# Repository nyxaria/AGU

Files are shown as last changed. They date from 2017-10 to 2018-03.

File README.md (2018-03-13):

# Autonomous Growing Unit

In this project I set out to create a robot that autonimously takes care of plants.<br>
The main goal was to learn as much as possible in as many areas I could, including software, hardware, electronics, CAD and even editing.

project video (https://vimeo.com/259930006)
<br><br>

Project Overview
----------------
The project is made up of 3 layers: The Android (High-level instructions), RaspberryPi 3 (High-level interpreter of instructions), and Arduino Mega (Low-level hardware controller).



The Android application is a simple UI composed of a rectangular 'garden' view where the user can add pots, and a 'seedbank' view where the user can select which seeds are in the physical trays of the machine. This application then communictes via Bluetooth with the RaspberryPi 3 [RPI], sending the raw data that the user put in. (Java)


<br><br>
The RPI acts as the brian of the operation, converting the high level abstracted instructions from the Android application into sequences of low level instructions, similar to GCODE, that the Arduino carries out one after another. It does this via scheduled timers as well as based on sensor data, such as the humidity soil sensor, depending on the plant.
It also makes a height map every day to monitor growth, personalise watering for each plant via plant-specific data scraped from a website (see Utility Programs.) (Python)
<br><br>
The Arduino firmware is the most low level code in this whole project, with the purpose of controlling the stepper motors on the gantry and probe, read end-stops, and turn the 2 pumps on/off. It communicates via the I2C bus with the Raspberry Pi 3, which acts as the brains of this build. (C++)

CAD
---
During this project I learnt to use Inventor, Fusion360, EAGLE as well as Fritzing. In the end, I ended up using Inventor instead of Fusion360 for the 3D model as it felt more natural to me (and more powerful) but used Fritzing and Eagle for the electronics diagram and schematic, respectively.

Model can be viewed online at https://skfb.ly/6vAEX.


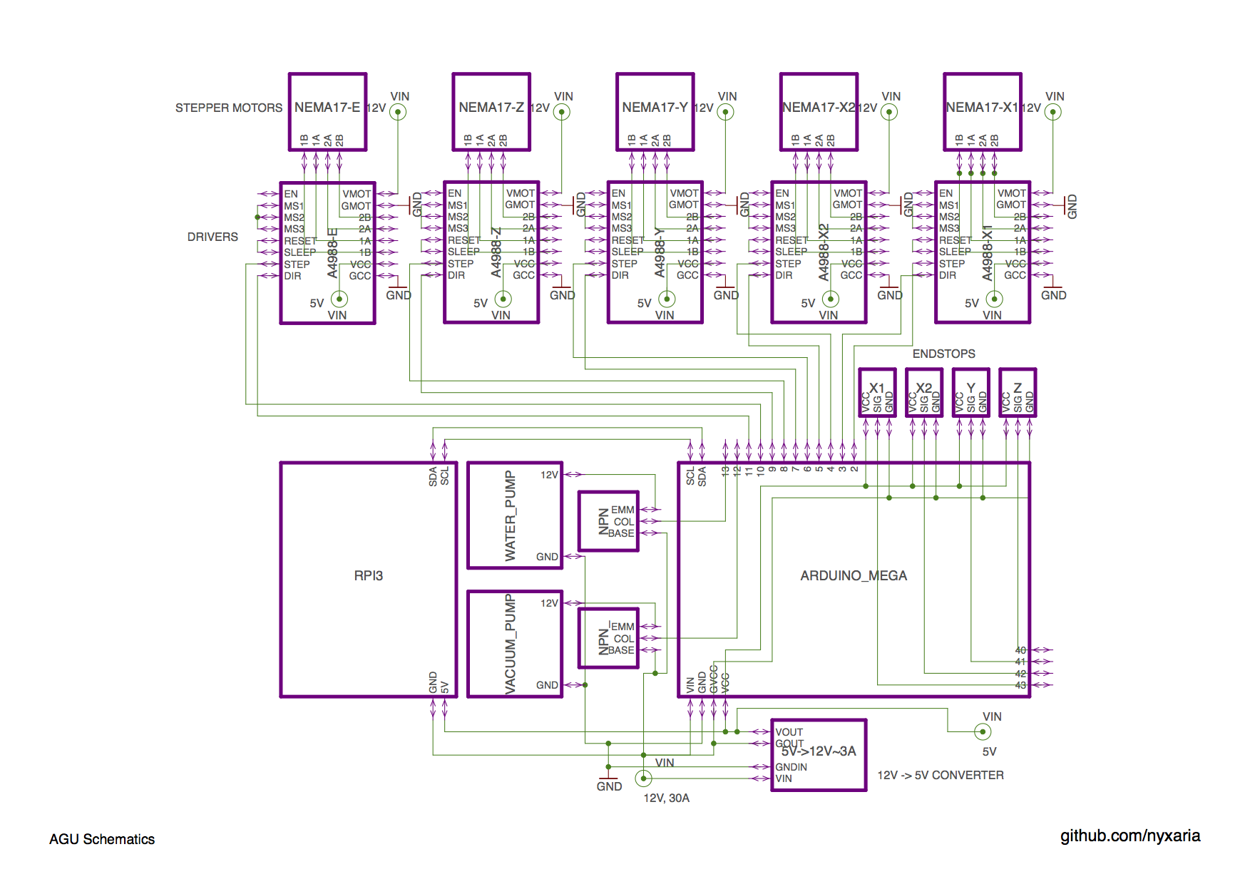
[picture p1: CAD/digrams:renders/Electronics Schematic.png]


Software
---

In this regard, I had alot of freedom in how I wanted to implement this. I ended up using an Arduino Mega because of the speed at which it alowed me to prototype, and the relative simplicity of the C++. In a future project, however, I will probably use an 8051/PIC/vanilla Atmel microcontroller and use Assembly or embedded C, not because I like self-inflicted pain but because it seems the only natural step in moving away from the 'hobby electronics' world. 
<br>In another direction I could use a ESP32 with it's Wifi+BT capabilities, and potentially eliminate the RPI entirely.
<br><br>
For the interface of the project I decided to make an Android application in Java (none of that Ionic nonsense) to brush up on my skills, but it could easily have been a Web interface written in JS+Html+Css for the UI and Flask+Py on the back end.

Hardware
---

I managed to get Makerbeams for free from my friend, so I used them for the construction. To hold everything together, I used tie plates from home depot. Everything else is held together by hot glue. For motion, I used bearings for z and x axis, and leadscrew for the y axis.

In this project I used Nema17 stepper motors which I managed to get for a really good price second hand. For the fluid transfer, I used a water pump from a coffee-machine and a vacuum pump from I ordered from China. The Mosfets and other components I scavenged from old electronics I got my hands on.

Electronics
---

I first created a schematic for project, and was planning on etching the PCB for the board containing the stepper motor drivers. However, none of the printers I have used to print the schematics on the toner-transfer paper in New York worked with the photo-transfer method. I presume it was because they were all Brother printers. As a result of that, I instead used a perf-board to make the driver break-out board.

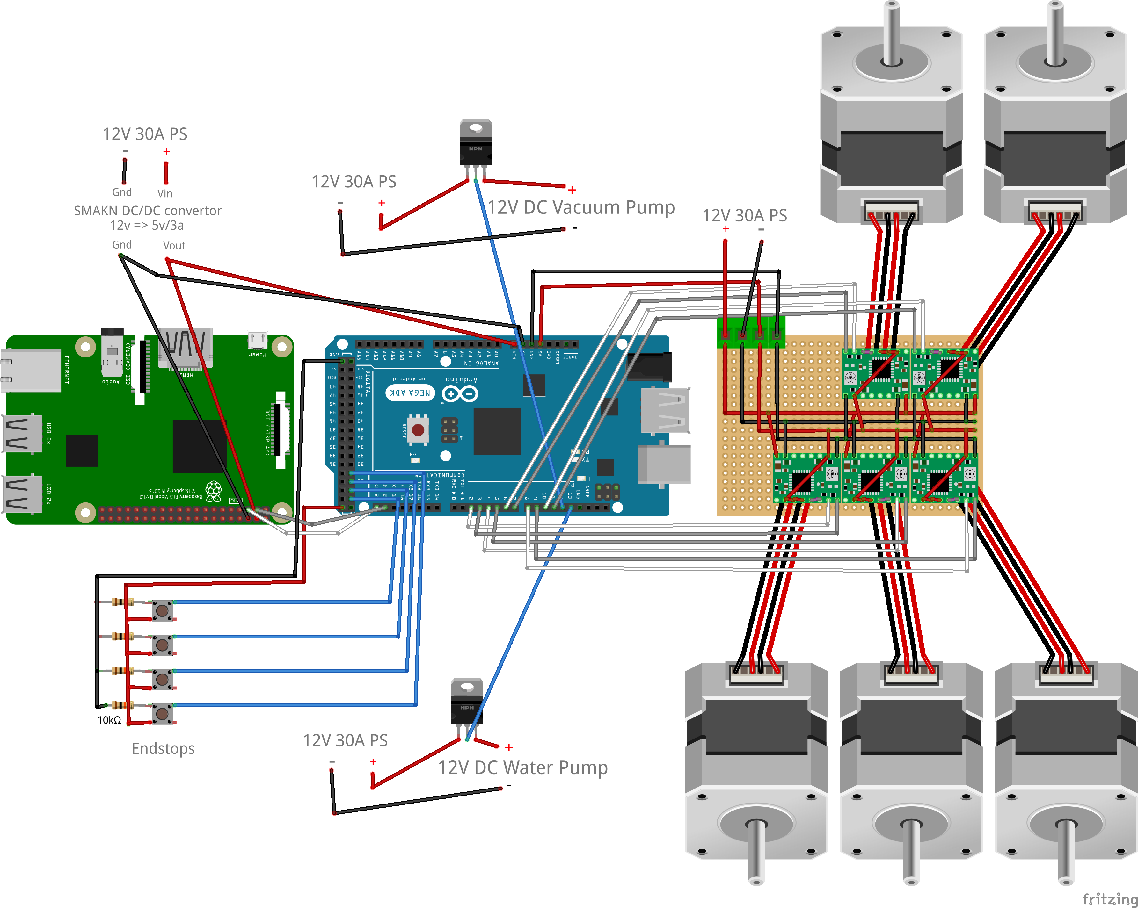
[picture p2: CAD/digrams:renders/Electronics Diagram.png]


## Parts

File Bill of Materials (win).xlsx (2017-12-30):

AGU Costs
Name | Link | Amount paid($) | Actual Cost ($) | Sum ($)
 | Electronics
Power cord | https://www.amazon.com/gp/product/B0022NH7G8/ref=oh_aui_detailpage_o06_s01?ie=UTF8&psc=1 | 8.77 |  | 240.71
12V30A PS | https://www.amazon.com/gp/product/B00D7CWSCG/ref=oh_aui_detailpage_o06_s01?ie=UTF8&psc=1 | 19.96
Arduino Mega 2560 + shield | https://www.ebay.com/itm/Arduino-Mega-2560-Board-with-Sensor-Shield-v2-0-Brand-New-Fast-Shipping/222626033269 | (Owned) | 14.24
12V -> 5V DC/DC converter | https://www.amazon.com/gp/product/B00CXKBJI2/ref=oh_aui_detailpage_o02_s00?ie=UTF8&psc=1 | 6.99
18AWG wire | https://www.amazon.com/gp/product/B00HZX4326/ref=oh_aui_detailpage_o06_s01?ie=UTF8&psc=1 | 6.68
RPI 3 | https://www.amazon.com/gp/product/B01CD5VC92/ref=oh_aui_detailpage_o07_s00?ie=UTF8&psc=1 | (Owned) | 35.46
Soil Humidity Sensor | https://www.ebay.com/itm/Soil-Humidity-Hygrometer-Moisture-Detection-Sensor-Module-Arduino-With-Wires-Hot-/401222026980 | 0.79
Nema 17 Steppers 10pcs | https://www.ebay.com/itm/10-x-Bipolar-Stepper-motor-NEMA-17-CNC-ROUTER-MILL-ROBOT-REPRAP-3D-printer/272831337324 | 41
Nema 17 Wires 10pcs | https://www.ebay.com/itm/10X-New-100cm-4-wire-Cable-For-Stepper-Motor-NEMA17-Shaft-For-5mm-CNC-Makerbot/142307586325 | 12.74
A4988 Drivers 5pcs | https://www.ebay.com/itm/5pcs-A4988-Stepper-Motor-Driver-Module-for-RepRap-3D-Printer/192024492415 | 8.89
Ultra sound sensor 5pc | https://www.ebay.com/itm/5Pcs-Ultrasonic-Module-HC-SR04-Distance-Measuring-Transducer-Sensor-Fo-Arduino/182711637444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 | 5.99
Dupont Wires | https://www.ebay.com/itm/T1-3X-40pcs-20cm-Male-To-Male-Female-Dupont-Wire-Jumper-Cable-Arduino-Breadboard/231708399395 | 5.99
12V Water pump | https://www.ebay.com/itm/Ultra-Quiet-Mini-DC-12V-Lift-3M-240L-H-Brushless-Motor-Submersible-Water-Pump/132087694620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 | 6.99
12V Vacuum pump | https://www.amazon.com/gp/product/B0192KPBCK/ref=oh_aui_detailpage_o01_s01?ie=UTF8&psc=1 | 19.99
Vero board x3 | https://www.ebay.com/itm/Prototyping-Board-2-x-4-3pcs-protoboard-perfboard-veroboard-arduino/322833594975 | 14
 | Hardware
10 ft 5/16” tube x2 | https://www.ebay.com/itm/10-Feet-of-5-16-I-D-Clear-Vinyl-Tubing-High-Quality-Food-Safe-Tubing/302021199236 | 13.98
Ball bearings 5mm bore 16mm dia 10pcs | https://www.ebay.com/itm/10pcs-Miniature-Deep-Groove-Ball-Bearing-625ZZ-5x16x5mm-HCXM/272824794694 | 14.24
GT2 Belt 2M + Pulley 20T 5mm bore x4 | https://www.ebay.com/itm/2m-2GT-6mm-Rubber-Pulley-Timing-Belt-2pcs-20T-Tooth-5mm-8mm-Gear-Pulley/401059027425 | 21.72
Brackets, 24x small, 4x big | Home Depot | 16
Nuts + Bolts + Washers | Home Depot | 6
Aluminium Extrusions | Open Build (1.5x1.5mm) 8x1000mm, 8x600mm (+ nuts and bolts) | (Gift) | ?
Luer lock needle set | https://www.amazon.com/gp/product/B01KZ0MHSC/ref=oh_aui_detailpage_o01_s00?ie=UTF8&psc=1 | 9.99

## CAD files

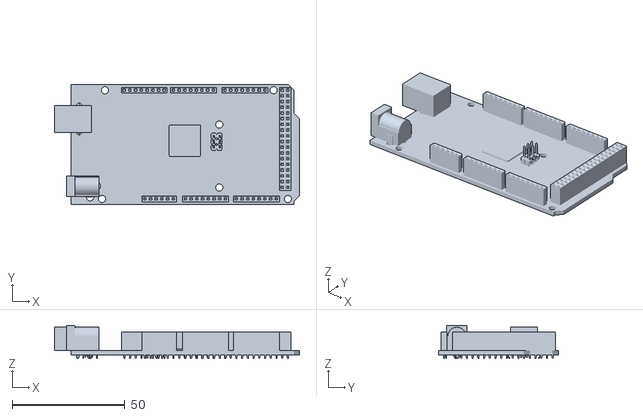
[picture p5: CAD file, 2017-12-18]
CAD/src/AGU_inventor/arduino-mega.stl
108.8 x 53.2 x 14.8

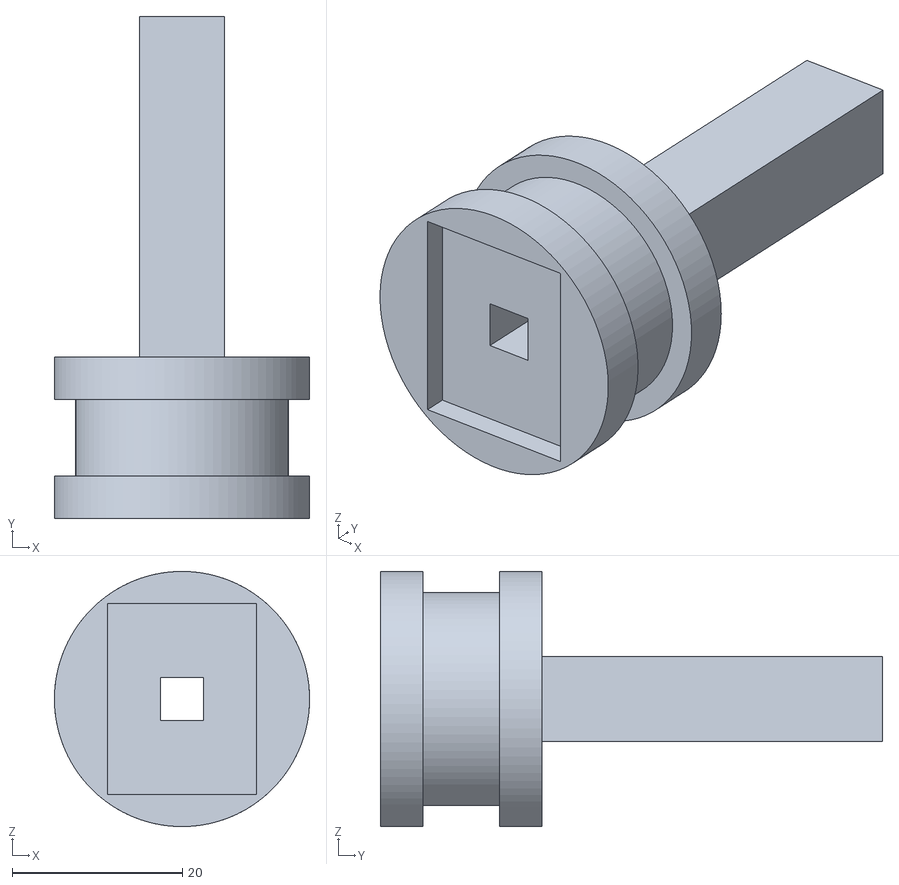
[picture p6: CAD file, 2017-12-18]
CAD/src/tool_mount.stl
30.0 x 59.0 x 30.0

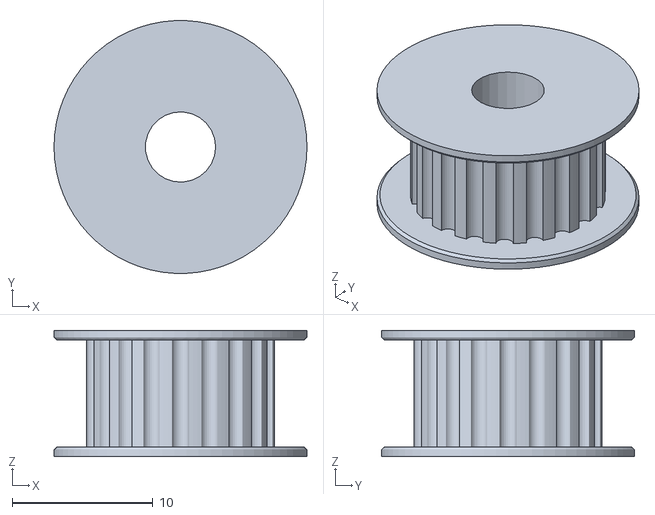
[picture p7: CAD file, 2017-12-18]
CAD/src/AGU_inventor/GT2Pulley-V3.stl
18.0 x 18.0 x 9.00

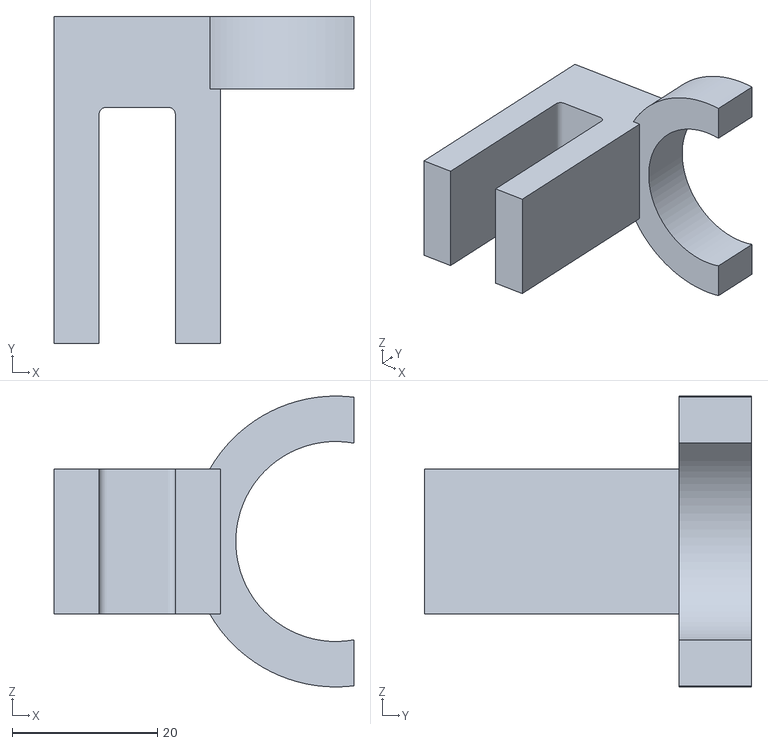
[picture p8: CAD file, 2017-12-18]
CAD/src/tool_holder.stl
41.2 x 45.0 x 40.0

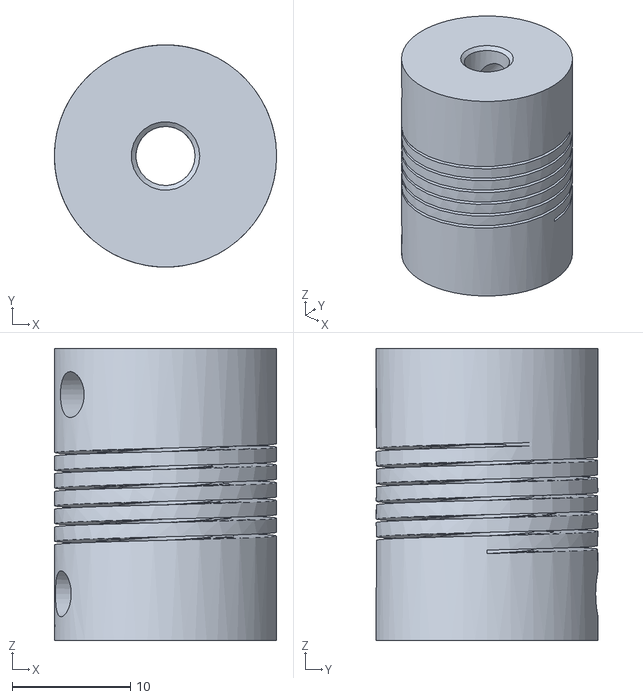
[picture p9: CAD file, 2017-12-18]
CAD/src/AGU_inventor/beam-coupling-5mm-8mm.stl
18.8 x 18.8 x 24.7

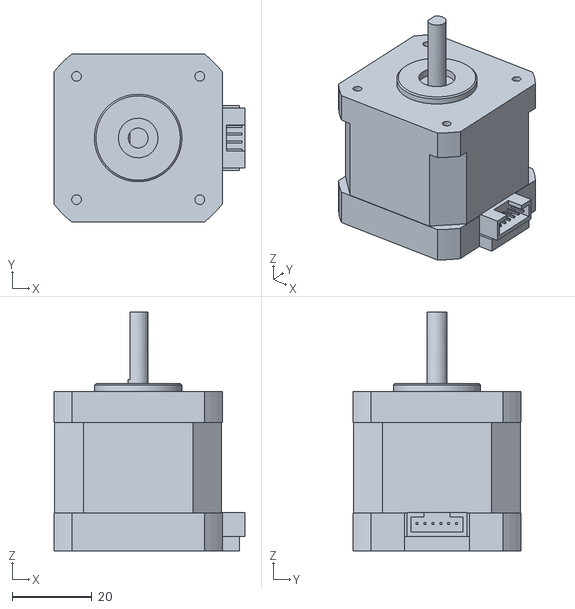
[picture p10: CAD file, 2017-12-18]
CAD/src/AGU_inventor/NEMA-17_Stepper_Motor_40mm_with_connector.stl
48.0 x 42.3 x 60.1

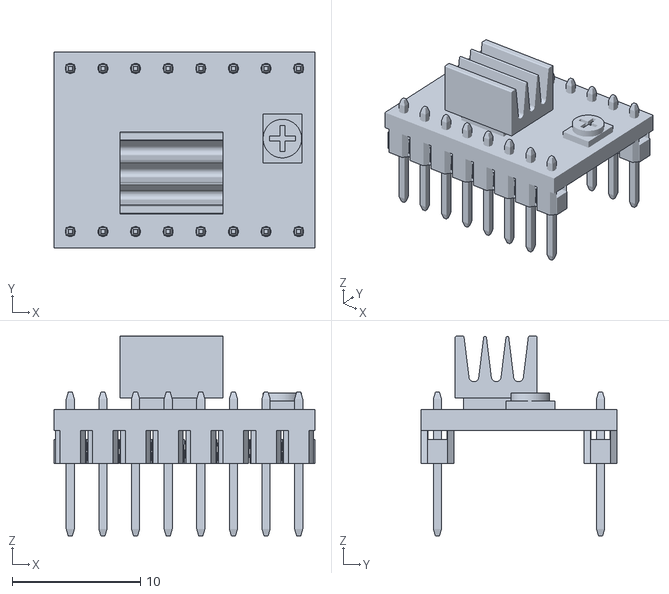
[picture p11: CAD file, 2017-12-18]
CAD/src/AGU_inventor/pololu-A500.stl
20.3 x 15.2 x 15.6

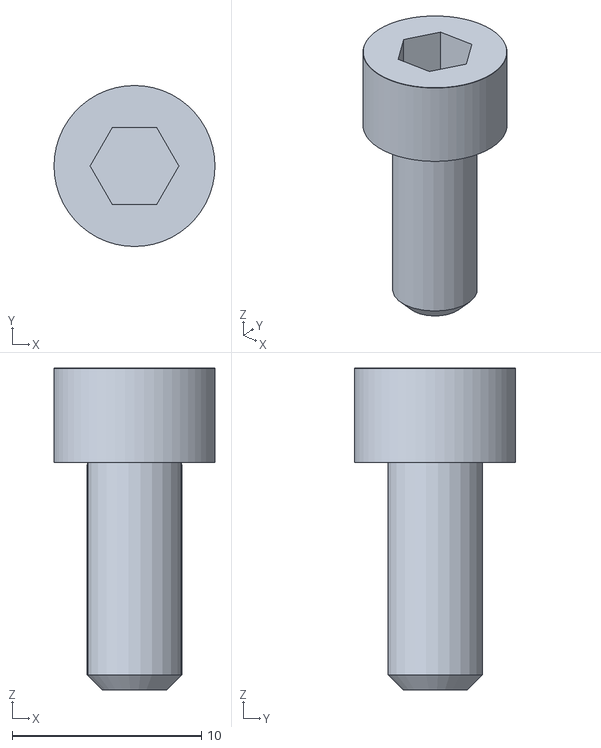
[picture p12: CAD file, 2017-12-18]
CAD/src/AGU_inventor/Screw M5x12 ISO4762 8,8 A2K.stl
8.50 x 8.50 x 17.0

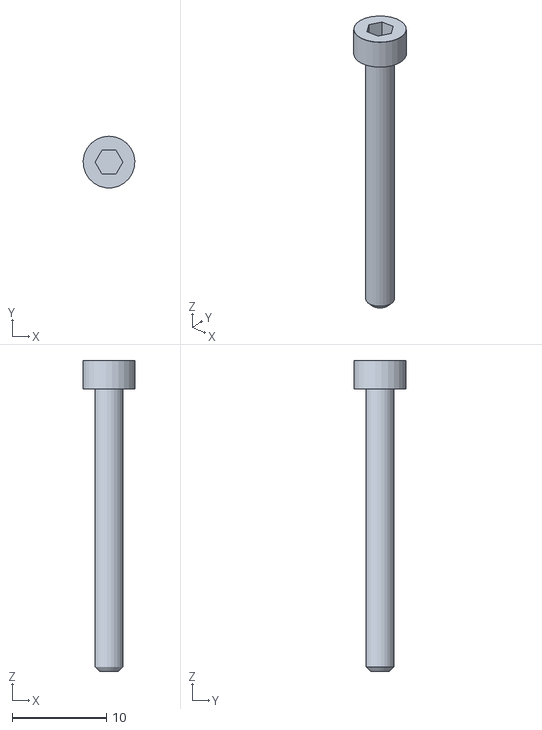
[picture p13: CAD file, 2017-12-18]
CAD/src/AGU_inventor/Screw M3x30 ISO4762 8,8 A2K.stl
5.49 x 5.48 x 33.0

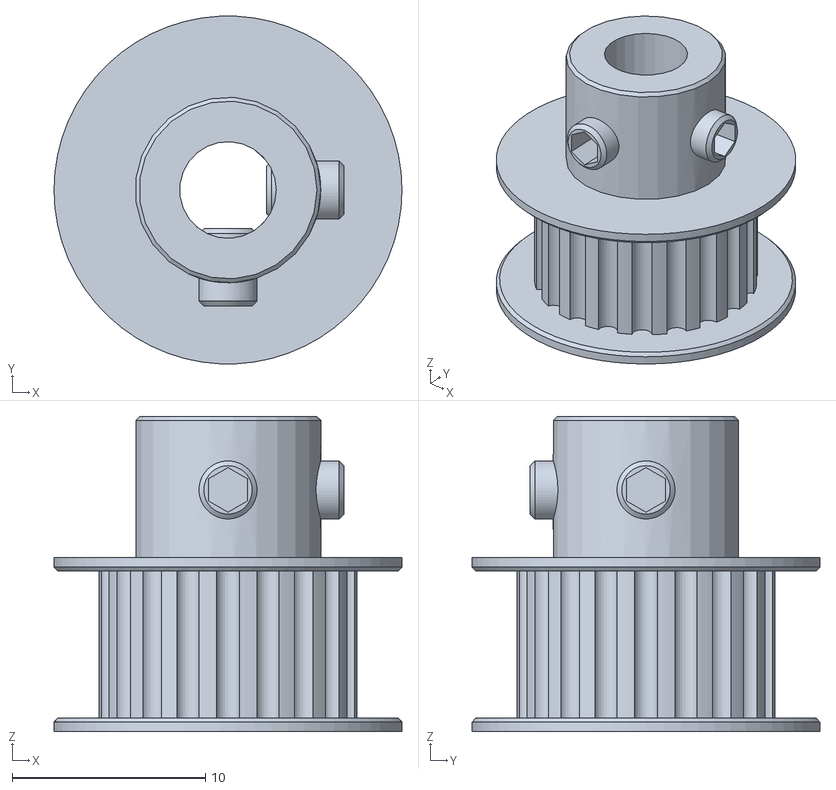
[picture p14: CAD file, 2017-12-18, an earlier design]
CAD/src/AGU_inventor/GT2Pulley-V2.stl
18.0 x 18.0 x 16.3

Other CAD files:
CAD/src/AGU_inventor/Trapezoidal_ thread.fcstd
CAD/src/AGU_inventor/5M nut 20mm.ipt
CAD/src/AGU_inventor/5M nut 20mm_MIR.ipt
CAD/src/AGU_inventor/5mm to 8mm holder.ipt
CAD/src/AGU_inventor/5mmx20mmx8mm bearing.ipt
CAD/src/AGU_inventor/5mmx20mmx8mm bearing_MIR.ipt
CAD/src/AGU_inventor/5mmx20mmx8mm bearing_MIR1.ipt
CAD/src/AGU_inventor/5mmx20mmx8mm bearing_MIR2.ipt
CAD/src/AGU_inventor/5mmx20mmx8mm bearing_MIR2_MIR.ipt
CAD/src/AGU_inventor/5mmx20mmx8mm bearing_MIR3.ipt
CAD/src/AGU_inventor/5mmx20mmx8mm bearing_MIR3_MIR.ipt
CAD/src/AGU_inventor/5mmx20mmx8mm bearing_MIR3_MIR_MIR.ipt
CAD/src/AGU_inventor/5x12 ISO4762 8,8 A2K.ipt
CAD/src/AGU_inventor/8M 900mm threaded rod.ipt
CAD/src/AGU_inventor/GT2Bearing metric.ipt
CAD/src/AGU_inventor/GT2Bearing metric_MIR.ipt
CAD/src/AGU_inventor/GT2Bearing.ipt
CAD/src/AGU_inventor/GT2Pulley metric.ipt
CAD/src/AGU_inventor/GT2Pulley metric_MIR.ipt
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

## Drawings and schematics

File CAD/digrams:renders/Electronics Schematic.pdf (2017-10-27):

## NEMA17-E

## NEMA17-Z

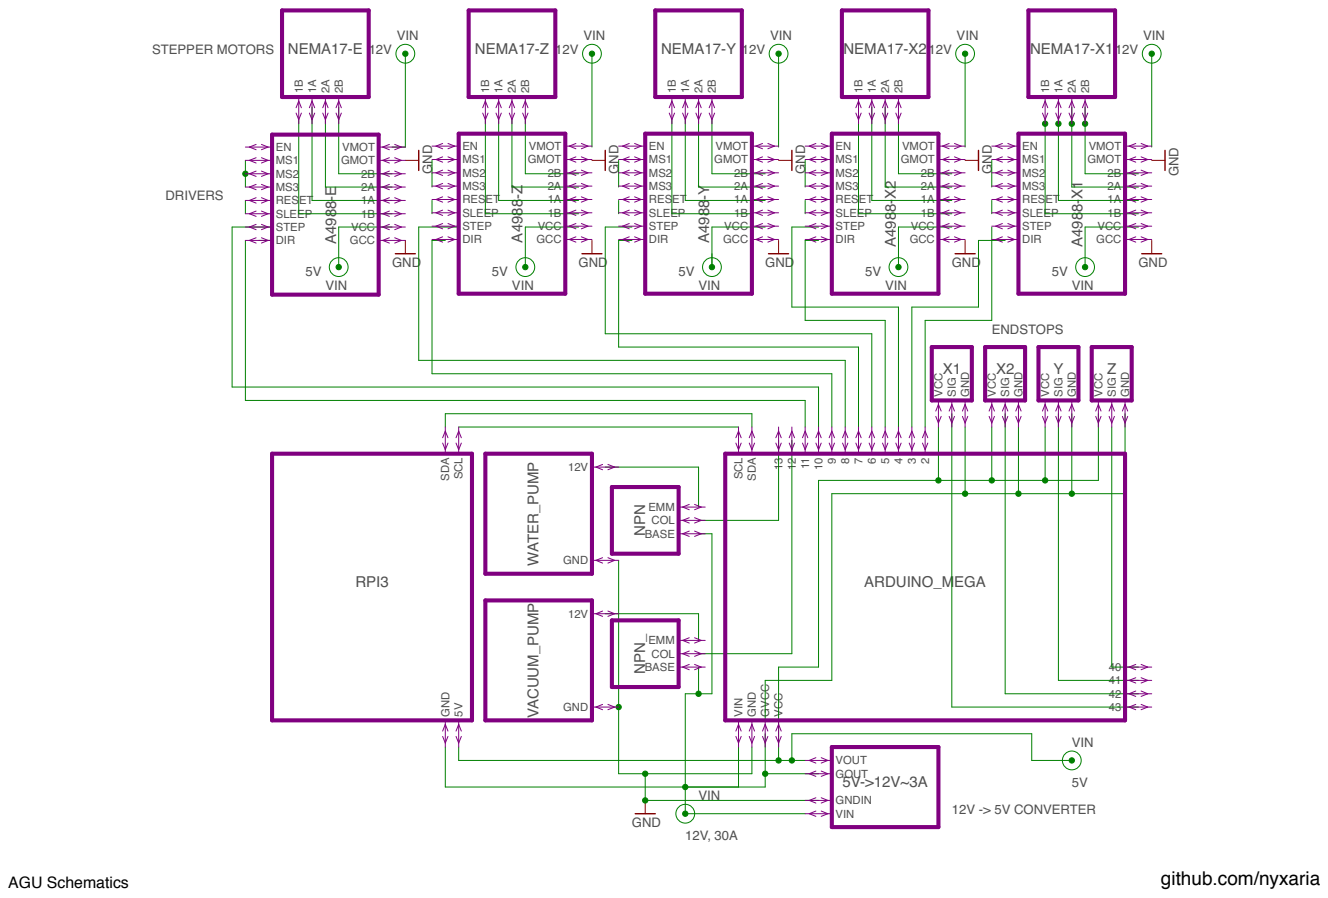
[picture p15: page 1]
GND; ENDSTOPS; 12V -> 5V CONVERTER; DRIVERS; STEPPER MOTORS; EN MS1 MS2 MS3 RESET SLEEP STEP DIR; VMOT GMOT 2B 2A 1A 1B VCC; GCC; A⁴⁹⁸⁸⁻Z; A⁴⁹⁸⁸⁻Y; A⁴⁹⁸⁸⁻X²; A⁴⁹⁸⁸⁻X¹; VMOT GMOT 2B 2A 1A 1B VCC GCC; ARDUINO_MEGA; VIN; GVCC; VCC; SCL; SDA; WAT; RPI3; COL BASE; EMM; NEMA17-Y; NEMA17-X2; NEMA17-X1; GNDIN; GOUT; VOUT; X1 VCC; SIG; X2 VCC; AGU Schematics; github.com/nyxaria

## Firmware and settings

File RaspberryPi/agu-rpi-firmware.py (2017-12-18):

import os
import subprocess
import glob
import time
import smbus
import pickle
from bluetooth import *
import threading
import datetime

server_sock=BluetoothSocket( RFCOMM )
server_sock.bind(("",PORT_ANY))
server_sock.listen(1)

CONTROLLER_REFRESH_RATE = 0.1;

bus = smbus.SMBus(1);

address = 0x01;
number = 0;
MAX_STRING_LENGTH = 30;
SEED_BANK = 50;
plantInfoPath = "/home/pi/Desktop/plantinfo";
potsPath = "/home/pi/Desktop/pots";
seedsPath = "/home/pi/Desktop/seeds";
metaDataPath = "/home/pi/Desktop/metaData";
width = 750;
height = 750;
pots = [];
seeds= [];
plants = {};
TYPE_RECT = 0;
TYPE_CIRCLE = 1;
offset = {};
positions = {};

port = server_sock.getsockname()[1]

uuid = "e77fa4a0-b21c-11e7-8f1a-0800200c9a66"
global toSend;
global commsThread;
global scheduleThread;
global controlThread;
global client_sock;
global meta;


def main():
        global commsThread, controlThread, scheduleThread;
        
        loadData();
        
        controlThread = threading.Thread(target=controllerThread);
        controlThread.start();
        scheduleThread = threading.Thread(target=scheduleThread);
        scheduleThread.start();

        initHardware();

        commsThread = threading.Thread(target=setUpComms);
        commsThread.start();

        
 
        
def connected():
        initFrontEnd();

## inits ##
        
def initHardware(): #on startup
        if(curX == 0 and curZ == 0): #dont home on origin
                moveTo(50,50,-1);
        home(False,False, True);
        home(True, True, False);
        print("\nHARDWARE READY");

        
def initFrontEnd(): #on BT connected
        prepareMeta();
        writeBtComms(meta);
        time.sleep(1);
        for seed in seeds:
                if(seed.seed != b'Empty'):
                        writeBtComms("SEED:"+str(seed)+":");
                        time.sleep(0.15);

        for pot in pots:
                writeBtComms("POT:"+str(pot)+":");
                time.sleep(0.1);
        
### -------------- ###

global now;
global next_start;

SCHEDULE_DAILY_HOUR = 20;

def scheduleThread():
        print("SCHEDULES READY\n---------");
        while True:
                now = datetime.datetime.now();
                next_start = datetime.datetime(now.year, now.month, now.day, SCHEDULE_DAILY_HOUR, 0, 0);
                if(now >= next_start):
                        next_start += datetime.timedelta(1);
                        tendCrops();

                time.sleep(60);

def tendCrops():
        if(len(pots) > 0):
                for pot in pots:
                        print("["+time.strftime("%H:%M:%S")+"] WATERING " + str(pot.seed) + " AT ("+ str(pot.x) +","+str(pot.y)+")")
                        waterPot(pot);
                        pot.active += 1;
                        
### Persistance + Data management ###

def save(mode):
        global pots, seeds;
        if(mode == 0): #pots
                file = open(potsPath, "wb");
                pickle.dump(pots,file);
                file.close();
        elif(mode == 1): #seeds
                file = open(seedsPath, "wb");
                pickle.dump(seeds,file)
                file.close();

        with open(metaDataPath, "r") as file:
                data = [line.rstrip("\n") for line in file];
        data[8] = currentAttachment;
        with open(metaDataPath, "w") as file:
                for item in data:
                        file.write("%s\n" % item);

def loadData():
        global pots, seeds, offset;
        prepareMeta();
        pots = [];
        seeds = [];
        filePots = open(potsPath, "rb");
        if(os.stat(potsPath).st_size != 0):
                pots = pickle.load(filePots);
        filePots.close();
        fileSeeds = open(seedsPath, "rb")
        if(os.stat(potsPath).st_size != 0):
                seeds = pickle.load(fileSeeds)
        fileSeeds.close();

        
        data = [line.strip("\n") for line in open(metaDataPath)];

        offset[SOIL_HUMIDITY_SENSOR] = int(data[0]);
        offset[ULTRA_SOUND_SENSOR] = int(data[1]);
        offset[VACUUM_BASE] = int(data[2]);
        offset[SCIENTIFIC_STICK] = int(data[3]);

        positions[ULTRA_SOUND_SENSOR] = data[4];
        positions[SOIL_HUMIDITY_SENSOR] = data[5];
        positions[VACUUM_BASE] = data[6];
        positions[SEED_BANK] = data[7]
        currentAttachment = int(data[8]);
        

def prepareMeta():
        global width,height;
        global plantInfoPath;
        global plants;
        global meta;
        meta = "META:";
        with open(plantInfoPath, 'r') as f:
            for line in f:
                    data = line.split(",");
                    if(data[0] != "Crop"):
                            plants[str(data[0])] = {};
                            plants[str(data[0])]["depth"] = int(data[1]);
                            plants[str(data[0])]["spacing"] = int(data[2]);
                            plants[str(data[0])]["water"] = data[3];
                            plants[str(data[0])]["vacuum_attachment"] = int(data[4]);
                            meta += data[0] + "~";
            f.close()

        meta = meta[:-1];
        meta += "," + str(width) + "~" + str(height);

### -------------- ###
        

### Hardware control ###

## Protocol constants

#motor node
motor = 0;

x1 = 0;
x2 = 1;
y = 2;
e = 3;
z = 4;

rotate = 0;
stop = 1;
speed = 2;
reset = 3;

ready = 5;

#read mpde
read = 1

soilHumidity = 0;
distance = 1;

#write node
write = 2;

wtr = 0;
_vacuum = 1;

on = 1;
off = 0;

#flags
DEFAULT = 0;
MOTOR_FINISHED = 50
MOTOR_RUNNING = 51;
DATA_RECEIVED = 125;
FAILURE = 126;
SUCCESS = 127;


#vars

NONE = -1;
ULTRA_SOUND_SENSOR = 0;
SOIL_HUMIDITY_SENSOR = 1;


VACUUM_BASE = 9;

GAUGE14_VACUUM = 10;
GAUGE16_VACUUM = 11;
GAUGE18_VACUUM = 12;
GAUGE20_VACUUM = 13;
GAUGE22_VACUUM = 14;
GAUGE25_VACUUM = 15;
GAUGE27_VACUUM = 16;
GAUGE30_VACUUM = 17;
SCIENTIFIC_STICK = 18;

VACUUM_ATTACHMENT_SPACING = 20;

currentAttachment = -1;
##
timeOn = 0;
waterActive = False;
delta_height = 600;
delta_hole = 2;
offset_attachment = 50;
seedbankSpacing = 22;

curX = 0;
curY = 0;
curZ = 0;

ATTACHMENTS_X = 0;
#Low level commands
def controllerThread():
        global timeOn, waterActive;
        while True:
                if(waterActive):
                        if(int(round(time.time()*1000)) - timeOn > 0):
                            timeOn = 0;
                            writeWater(off,0);
                            waterActive = False;

def flush():
        writeI2CData([motor, ready]);

def homeMotor(motorCode): #int 
        global curY, curZ, curY;
        writeI2CData([motor, motorCode, reset]);
        if(motorCode == x1 or motorCode == x2):
                curX = 0;
        elif(motorCode == z):
                curZ = 0;
        elif(motorCode == y):
                curY = 0;

def moveMotorTo(motorCode, distMM): #int, int
        global curY, curZ, curY;
        low = distMM%255;
        high = distMM//255;

        if(low == 255 or low == 254): #255 and 254 = start and end of bit flags
                low = 0; #error = 2mm in worst case , worth redoing ? strict packet format. 
                high += 1;
        
        writeI2CData([motor, motorCode, rotate, high, low]);
        if(motorCode == x1 or motorCode == x2):
                curX = distMM;
        elif(motorCode == z):
                curZ = distMM;
        elif(motorCode == y):
                curY = distMM;

def stopMotor(motorCode): #int
        writeI2CData([motor, motorCode, stop]);

def speedMotor(motorCode, percentage): #int, int
        writeI2CData([motor, motorCode, percentage]); 

def writeWater(state, t): #int, int
        global timeOn, waterActive;
        if(t != -1):
                if(state == on):
                        waterActive = True;
                        timeOn = int(round(time.time()*1000 + t))
        writeI2CData([write, wtr, state]);

def writeVacuum(state): #int
        writeI2CData([write, _vacuum, state]);

def readHumidity():
        writeI2CData([read, soilHumidity]);

def readDistance():
        writeI2CData([read, distance]);

def waitMotorFinished():
        while True:#
                if(readI2CByte() == MOTOR_FINISHED):
                        break;

def waitActionFinished():
        while True:
                if(readI2CByte() != DATA_RECEIVED):
                        break;
                
#Medium-level Commands/Sequences

def vacuum(state):
        writeVacuum(state);
        waitActionFinished();

def water(state, t):
        writeWater(state, t);
        waitActionFinished();

def getSoilHumidity():
        readHumidity();
        waitActionFinished();
        return readI2CByte();
def getDistance():
        readDistance();
        waitActionFinished();
        pot.height = readI2CByte();

def moveTo(targetX, targetZ, targetY):
        if(targetX != -1):
                moveMotorTo(x1, targetX);
                moveMotorTo(x2, targetX);
        if(targetZ != -1):
                moveMotorTo(z, targetZ);
        if(targetY != -1):
                moveMotorTo(y, targetY);
        flush();
        waitMotorFinished();

def home(homeX, homeZ, homeY):
        if(homeX):
                homeMotor(x1);
                homeMotor(x2);
        if(homeZ):
                homeMotor(z);
        if(homeY):
                homeMotor(y);
        flush();
        waitMotorFinished();
        if(homeY):
                moveTo(-1,-1,10)


def moveToAttachment(attachment):
        global currentAttachment, positions;
        if(currentAttachment == attachment):
                return;


        if(attachment == ULTRA_SOUND_SENSOR):
                xOff = 16;
                zOff = 1 
                moveTo(59 + xOff,191 + zOff,525);
                
                moveTo(44 + xOff ,190+ zOff,565);
                
                moveTo(30-5+ xOff,208 + zOff,578);
                moveTo(30-5,205,581);
                moveTo(65,203,578);
                moveTo(-1,-1,520);
                moveTo(59+xOff, 191 + zOff, 505)
                
                currentAttachment = attachment;

                return;
        if(attachment == SOIL_HUMIDITY_SENSOR):
                moveTo(39,256,525);
                moveTo(40,255,565);
                moveTo(34,265,580);
                moveTo(31,265,582);
                moveTo(60,265,580);
                moveTo(60,280,575);
                moveTo(47,280,575);
                moveTo(60,280,575);
                moveTo(60,280,550);
                moveTo(39,256,525);
                currentAttachment = attachment;
                return;

        #this dosen't work =( ah the optimism of a software guy.
        pts = [];
        if(attachment > 9 and attachment < 20):
                pts += positions[VACUUM_BASE].split(",");
                print(pts);
                moveTo(int(str(pts[0])), int(str(pts[1])) + (attachment - 10)*VACUUM_ATTACHMENT_SPACING, -1);
        moveTo(-1, -1, int(str(pts[2])));

        
        elif(attachment > 9 and attachment < 20):
                vacuum(on);
                time.sleep(1);

        moveTo(-1, -1, int(str(pts[2])) - offset_attachment);

        
def depositAttachment(attachment):
        global currentAttachment, positions;
        if(currentAttachment == NONE and attachment < 9):
                return;

        if(attachment == ULTRA_SOUND_SENSOR):
                xOff = 16;
                zOff = 1 
                moveTo(59 + xOff,200 + zOff,525);
                moveTo(80,200+zOff,578);
                moveTo(30-5+ xOff,202 + zOff,576);
                moveTo(-1,-1,520);                
                moveTo(59 + xOff,191 + zOff,525);
                currentAttachment = NONE;

                return;
        if(attachment == SOIL_HUMIDITY_SENSOR):
                xOff = 16;
                zOff = 41; 
                moveTo(59 + xOff,200 + zOff,525);
                moveTo(80,200+zOff,578);
                moveTo(30-5+ xOff,202 + zOff,576);
                moveTo(-1,-1,520);                
                moveTo(59 + xOff,191 + zOff,525);
                currentAttachment = NONE;
                return;


        pts = [];
        if(attachment > 9 and attachment < 20):
                pts += positions[VACUUM_BASE].split(",");
                moveTo(int(str(pts[0])), int(str(pts[1])) + (attachment - 10)*VACUUM_ATTACHMENT_SPACING, -1);
        
        moveTo(-1, -1, int(str(pts[2])));

        if(attachment > 9 and attachment < 20):
                vacuum(off);
                time.sleep(1);

        moveTo(-1, -1, int(str(pts[2])) - offset_attachment);

    
def waterPot(pot):
        global pots, plants;
        targetX = 0;
        targetY = 0;
        water = plants[str(pot.seed)[2:-1]]["water"];
        radius = 0;

        if(pot.Type == TYPE_RECT):
                targetX = pot.x + (pot.xDim/2);
                targetY = pot.y + (pot.yDim/2);
                radius = min(pot.xDim/4, pot.yDim/4);
        elif(pot.Type == TYPE_CIRCLE):
                targetX = pot.x;
                targetY = pot.y;
                radius = min(pot.xDim/2, pot.yDim/2);


        if(currentAttachment != ULTRA_SOUND_SENSOR):
                depositAttachment();
                moveToAttachment(ULTRA_SOUND_SENSOR);

        home(False, False, True);
        moveTo(targetX + radius, targetY + radius, -1);

        if(pot.height == 0):
                pot.height = getDistance() - offset[ULTRA_SOUND_SENSOR];
                pot.archive += [pot.height];
        else:
                pot.archive += [getDistance() - offset[ULTRA_SOUND_SENSOR]];

        depositAttachment(currentAttachment);
        moveToAttachment(HUMIDITY_SOIL_SENSOR);

        home(False, False, True);
            
        pot.water = 0;
        moveTo(targetX + radius, targetY + radius, -1);

        if(water == "nd"):
                while(pot.water < pot.threshold):
                        moveTo(-1, -1, 300);
                        water(on, -1);

                        moveTo(targetX - radius, targetY + radius);
                        moveTo(targetX - radius, targetY - radius);
                        moveTo(targetX + radius, targetY - radius);
                        moveTo(targetX + radius, targetY + radius);

                        water(off, -1);
                        time.sleep(10);

                        moveTo(-1, -1, pot.height - offset[SOIL_HUMIDITY_SENSOR]);
                        pot.water = getSoilHumiditiy();
                
        else:
                water(on,int(round(float(pot.water)/float(float(240)/1000/60/60))));
                
                while(int(round(time.time()*1000)) - timeOn > 0):
                        if(waterActive):
                                break;
                        moveTo(targetX - radius, targetY + radius);
                        if(waterActive):
                                break;
                        moveTo(targetX - radius, targetY - radius);
                        if(waterActive):
                                break;
                        moveTo(targetX + radius, targetY - radius);
                        if(waterActive):
                                break;
                
                time.sleep(10);
                moveTo(-1, -1, pot.height - offset[SOIL_HUMIDITY_SENSOR]);
                pot.water = getSoilHumidity();

        home(False, False, True);
        pot.dayCount += 1;
            

def seedPot(pot):
        global pots, plants;
        targetX = 0;
        targetY = 0;
        depth = plants[pot.seed]["depth"];

        if(pot.Type == TYPE_RECT):
                targetX = pot.x + (pot.xDim/2);
                targetY = pot.y + (pot.yDim/2);
        elif(pot.Type == TYPE_CIRCLE):
                targetX = pot.x;
                targetY = pot.y;

        if(pot.height == 0):
                if(currentAttachment != ULTRA_SOUND_SENSOR):
                        depositAttachment(currentAttachment);
                moveToAttachment(ULTRA_SOUND_SENSOR);

                home(False, False, True);
                moveTo(targetX, targetY, -1);
                
                pot.height = getDistance() - offset[ULTRA_SOUND_SENSOR];
                pot.archive += [pot.height];

        
        depositAttachment(currentAttachment);

        home(False, False, True);
        moveToAttachment(plants[pot.seed]["vacuum_attachment"]);
        getSeed(pot.seed);

        home(False, False, True);
        moveTo(targetX, targetY, -1);
        moveTo(-1,-1, pot.height - offset[VACUUM_BASE] + depth-10);
        vacuum(off);
        moveTo(-1,-1, pot.height - offset[VACUUM_BASE] + depth+5);
        moveTo(-1,-1, pot.height - offset[VACUUM_BASE] + depth+10);
        vacuum(on);
        ###

        home(False, False, True);
        depositAttachment(plants[pot.seed]["vacuum_attachment"]);

        vacuum(off);

def getSeed(seed):
        for seedbank in seeds:
                if(seedbank.seed == seed):
                        pts = positions[VACUUM_BASE].split(",");
                        moveTo(int(str(pts[0])), int(str(pts[1])) + seedbank.index*seedbankSpacing, -1);
                        moveTo(-1, -1, int(str(pts[2])));
                        vacuum(on);
                        
### I2C Comms ###

def writeI2CByte(value):
    bus.write_byte(address, int(value));


def readI2CByte():
    try:
        return(bus.read_byte(address));
    except IOError:
        print("error");
    return number

def writeI2CData(data):
    if(data == []):
            return;

    try:
            writeI2CByte(255); #flag start

            for byte in data:
                    writeI2CByte(byte);

            writeI2CByte(254); #flag end
            print("I2C-send: '{}' to address {}".format(data, hex(address)));
   
            returnCode = readI2CByte();
            print("\t Response = {}".format(returnCode));
    except IOError:
            print("ioerror");
            subprocess.call(["i2cdetect","-y","1"]);
            writeI2CData(data);
            print("trying again");
    #return returnCode;

###

        
### Bluetooth Comms ###

def setUpComms():
        global connected;
        global client_sock;
        advertise_service( server_sock, "AGU",
				   service_id = uuid,
				   service_classes = [ uuid, SERIAL_PORT_CLASS ],
				   profiles = [ SERIAL_PORT_PROFILE ],
#                   protocols = [ OBEX_UUID ]
					)
        while True:
                print("Waiting for connection on RFCOMM channel %d" % port)

                client_sock, client_info = server_sock.accept()
                print("Accepted connection from "+ ''.join(map(str,client_info))+"\n-------")
                connected();
                try:
                        while True:
                                data = client_sock.recv(1024)
                                if len(data) != 0:
                                        processBtData(data);

                except IOError:
                        pass

def writeBtComms(data):
        global client_sock;
        client_sock.send(data);
        print("BT-send: "+data+"\n");
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

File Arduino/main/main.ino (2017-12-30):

#include "I2C.h"
#include "RAP.h"
#include "MotorHandler.h"
#include "SensorHandler.h"

SensorHandler sensorHandler;
MotorHandler motorHandler;
I2C i2c;
RAP rap; //raspberry pi - arduino - protocol (names are not my strong point)

void setup() {
    pinMode(38, OUTPUT); //water
    pinMode(32, OUTPUT); //vacuum
    digitalWrite(32, LOW);
    digitalWrite(38, LOW);

    i2c.init();
    motorHandler.init();
    rap.motors = &motorHandler;
    rap.sensors = &sensorHandler;
   
}
long delayMs = millis();
int toSend = 0;
void loop() {
    if (i2c.ready()) { //check for data from rpi
        i2c.send(rap.handleRequest(i2c.get())); //run process and respond to rpi
        delayMs = millis();
    }
    if(millis() - delayMs > 100) { //send constant flag for RPI except when requesting information
        i2c.send(motorHandler.finished());
    }
    motorHandler.tick();
}

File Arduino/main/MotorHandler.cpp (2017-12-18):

#include "Arduino.h"
#include "MotorHandler.h"
#include "Motor.h"
#include "RAP.h"

#define X1_STEP_PIN 2
#define X1_DIR_PIN  3
#define X1_ENDSTOP_PIN 42

#define X2_STEP_PIN 8
#define X2_DIR_PIN  9
#define X2_ENDSTOP_PIN 43

#define Y_STEP_PIN 10
#define Y_DIR_PIN  11
#define Y_ENDSTOP_PIN 52

//#define E_STEP_PIN 6
//#define E_DIR_PIN  7

#define Z_STEP_PIN 6
#define Z_DIR_PIN  7
#define Z_ENDSTOP_PIN 40

float stepsPerMM_LEADSCREW = 141.73*8.0/9.0;




Motor x1;
Motor x2;
Motor y;
Motor z;
//Motor e;
MotorHandler::MotorHandler() {

}

void MotorHandler::init() {
    x1.init(X1_STEP_PIN, X1_DIR_PIN, X1_ENDSTOP_PIN, Motor::stepsPerMM_TIMING_BELT);
    x2.init(X2_STEP_PIN, X2_DIR_PIN, X2_ENDSTOP_PIN, Motor::stepsPerMM_TIMING_BELT);
   
    y.init(Y_STEP_PIN, Y_DIR_PIN, Y_ENDSTOP_PIN, stepsPerMM_LEADSCREW);
    z.init(Z_STEP_PIN, Z_DIR_PIN, Z_ENDSTOP_PIN, Motor::stepsPerMM_TIMING_BELT);
    //e.init(4,E_STEP_PIN, E_DIR_PIN, -1, Motor::stepsPerMM_GEAR);
}

Motor* MotorHandler::get(byte key) {
  switch (key) {
    case MotorHandler::m_x1:
      return &x1;
      break;
    case MotorHandler::m_x2:
      return &x2;
      break;
    case MotorHandler::m_y:
      return &y;
      break;
    case MotorHandler::m_z:
      return &z;
      break;
//    case MotorHandler::m_e:
      //return &e;
//      break;
  }
  return 0;
}

void MotorHandler::tick() { //update logic
    
  x1.tick();
  x2.tick();
  y.tick();
  //e?.tick();
  z.tick();

 
}

void MotorHandler::ready(bool b) {
    x1.ready = x2.ready = y.ready = z.ready = b;
}


byte MotorHandler::finished() {
    if(!x1.busy && !x2.busy && !y.busy && !z.busy) {
        return RAP::MOTOR_FINISHED;
    } else {
        return RAP::MOTOR_RUNNING;
    }
}

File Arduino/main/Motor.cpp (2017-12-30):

#include "Arduino.h"
#include "Motor.h"
#include "MotorHandler.h"
#include "RAP.h"
#include "SensorHandler.h"
#include <AccelStepper.h>
#include <stdlib.h>     /* abs */
#include <math.h>

void Motor::init(byte sPin, byte dPin, byte pES, int sPmm) {
    stepsPerMM = sPmm;
    endStopPin = pES;
    s._interface = 1;
    s._pin[0] = sPin;
    s._pin[1] = dPin;
    stepPin = sPin;
    dirPin = dPin;
    s.enableOutputs();
    s._targetPos = s._currentPos = 0;
    if(stepPin == 10)
        pinMode(pES, INPUT_PULLUP);
    else
        pinMode(pES, INPUT);

    if(sPin == 8) {
        s.setPinsInverted(true);
    }
    
    if(sPin == 10) { // y dir does not have 16 micro stepping enabled
        s.setMaxSpeed(2000/4);
        s.setSpeed(2000/4);
        s.setAcceleration(1000/4);
    } else {
        s.setMaxSpeed(2000);
        s.setSpeed(2000);
        s.setAcceleration(1000);
    }
   
}


int Motor::enqueue(byte* req) {
    switch(req[2]) {
        case RAP::rotate:
            return rotate((byte)req[3], (byte)req[4]);
            break;
        case RAP::speed:
            return speed((byte)req[3]); // 0 - 100 % of pre-determined maxSpeed
            break;
        case RAP::stop:
            return stop();
            break;
        case RAP::reset:
            return reset();    
        default:
            return RAP::FAILURE;
  }
}

void Motor::tick() {
   if(ready) {
       if(homing) {
            s.run();
            if((stepPin == 10 && digitalRead(endStopPin) == LOW) || (stepPin != 10 && digitalRead(endStopPin) == HIGH)) {
                if(timer == 0) 
                    timer = millis();
                
                if((millis() - timer > 10 && stepPin != 10) || (millis() - timer > 5 && stepPin == 10)) {
                    s.stop();
                    s.runToPosition();
                    s._targetPos = s._currentPos = 0;

                    timer = 0;
                    homing = false;
                    busy = false;
                    complete = true;
    
                    if(stepPin == 10) { // y dir does not have 16 micro stepping enabled
                        s.setMaxSpeed(2000/4);
                        s.setSpeed(2000/4);
                        s.setAcceleration(1000/4);
                    } else {
                        s.setMaxSpeed(2000);
                        s.setSpeed(2000);
                        s.setAcceleration(1000);
                    }
                }
            } else {
                timer = millis();
            }
       } else {
            if(s._targetPos != s._currentPos) {       
                s.run();
            }
            busy = !(s._targetPos == s._currentPos);
       }
   }
}


int Motor::rotate(byte high, byte low) {
    complete = false;
    busy = true;
    homing = false;
    long mm = high*((long)255) + low;
    //double toDo = 0.0;
    //leftOverSteps += modf(leftOverSteps, &toDo);

    s.moveTo(-abs((long)((mm/* + toDo*/)*stepsPerMM)));

    return RAP::SUCCESS;

}

int Motor::speed(byte percentage) {
    s.setMaxSpeed((percentage * Motor::maxSpeed) / 100);
    s.setSpeed((percentage * Motor::maxSpeed) / 100);
    s.setAcceleration((percentage * Motor::maxSpeed) / 200);
    return RAP::SUCCESS;
}


int Motor::stop() {
    s.stop();
    s._targetPos = s._currentPos;
    busy = false;
    return RAP::SUCCESS;
}

int Motor::reset() {
    complete = false;
    busy = true;
    homing = true;
    s.stop(); 

    if(stepPin != 10) {
        s.setMaxSpeed(1000);
        s.setSpeed(500);
        s.setAcceleration(500);
    } else {
        s.setMaxSpeed(250);
        s.setSpeed(250);
        s.setAcceleration(500);
    }
    s.move(1000000);

    return RAP::SUCCESS;
}

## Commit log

2017-10-27 Intial commit
    Includes:
    CAD:Electronics[schematic+diagram]
    Software:Arduino(90%done)
    Bill of Materials
2017-11-16 finished arduino firmware
    added sensors,
    revamped comms. protocols.
2017-12-18 finished project!!!
    [5M nut 20mm.0002.ipt, 5M nut 20mm.0003.ipt, 5M nut 20mm.ipt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]
2017-12-30 cleaned up dirs
    [Bill of Materials (win).xlsx, pulley_shutter.stl, tool_holder.stl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]
2017-12-31 added png of schematics
